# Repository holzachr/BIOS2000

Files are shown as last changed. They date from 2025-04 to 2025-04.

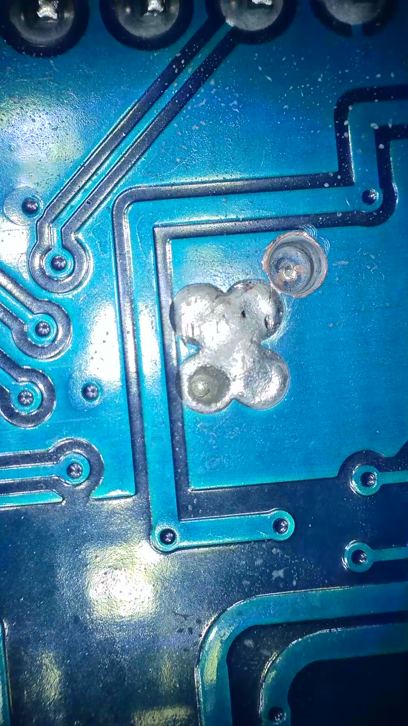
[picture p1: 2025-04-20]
Hardware/MFRC522 RFID module modification for I2C bus/MFRC522_I2C_mod_3.jpg

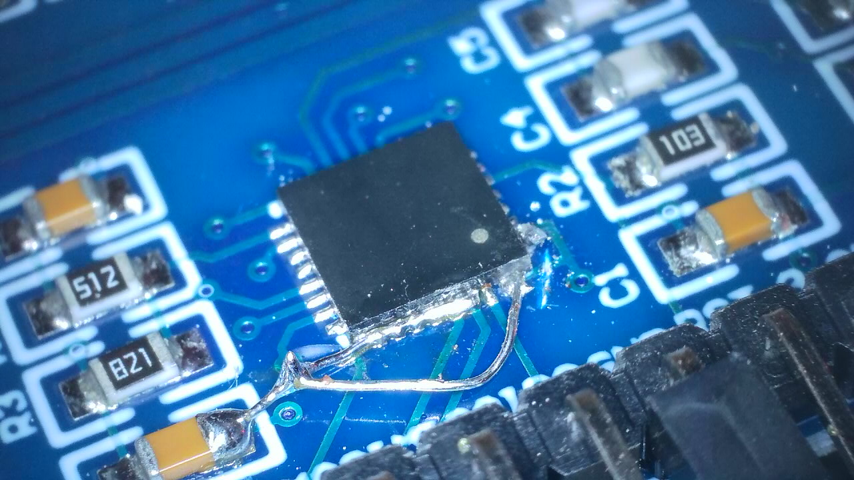
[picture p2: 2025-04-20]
Hardware/MFRC522 RFID module modification for I2C bus/MFRC522_I2C_mod_1.jpg

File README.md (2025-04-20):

# BIOS 2000
## An open-source cocktail machine and shot dispenser

- Peristaltic pumps are used to deliver liquids from bottles, 6 in this case, through 3x5 mm (inner and outer diameter) silicon hoses to an output.
- A simple web interface can be used to compose mixed drinks or just dispense shots.
- An RFID reader offers an "instant shot mode" after the tag has been read and a button pressed.

## Hardware

Main controller of this project is an ESP8266 "NodeMCU" module, programmed through the Arduino IDE.

The type G528 pumps are available in different sizes, 6 and 12 V, and different speeds. Because even the largest pump is quite slow in terms of typical drink volume, you want to get the biggest 150 ml/s 12 V variant.

Each two pumps are driven by a L298N H-bridge, and each H-Bridge is controlled by two GPIO lines.

To save GPIO lines from the ESP module, PCF8574 I2C-to-GPIO expanders are used, but this is generally optional.

The MFRC522 RFID reader modules generally only support SPI modes, but can be modified in order to use their I2C bus. This requires some fine soldering skills - check out the "Hardware" directory.

A LED strip offers fancy lighting.

Because my machine case is an old PC case, I repurposed the HDD activity LED to flicker randomly when the machine is working.

## ESP/Arduino libraries

- https://github.com/me-no-dev/ESPAsyncWebServer for the web server
- https://github.com/me-no-dev/ESPAsyncTCP for WebSocket
- https://github.com/bblanchon/ArduinoJson for data exchange between Arduino and web code
- https://github.com/RobTillaart/PCF8574/ for the IO expanders
- https://github.com/arozcan/MFRC522-I2C-Library/ for the RFID reader
- https://github.com/FastLED/FastLED for an optional LED strip

## Pump calibration

The pump variation is quite large, and you want to make sure that the drinks don't spill over.
That's what the calibration.html website on the ESP is for:
You dispense a drink, say 300 ml, from each pump. You measure or weight how much you actually got, and use the calibration.html website to calculate individual per-pump ml/s values, which are compiled into the code (nasty).
Make sure you adapt those constants to your individual pumps.

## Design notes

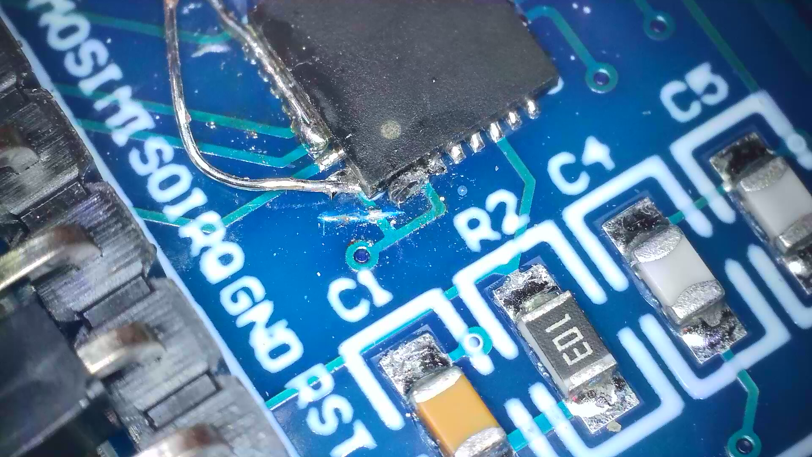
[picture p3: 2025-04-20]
Hardware/MFRC522 RFID module modification for I2C bus/MFRC522_I2C_mod_2.jpg

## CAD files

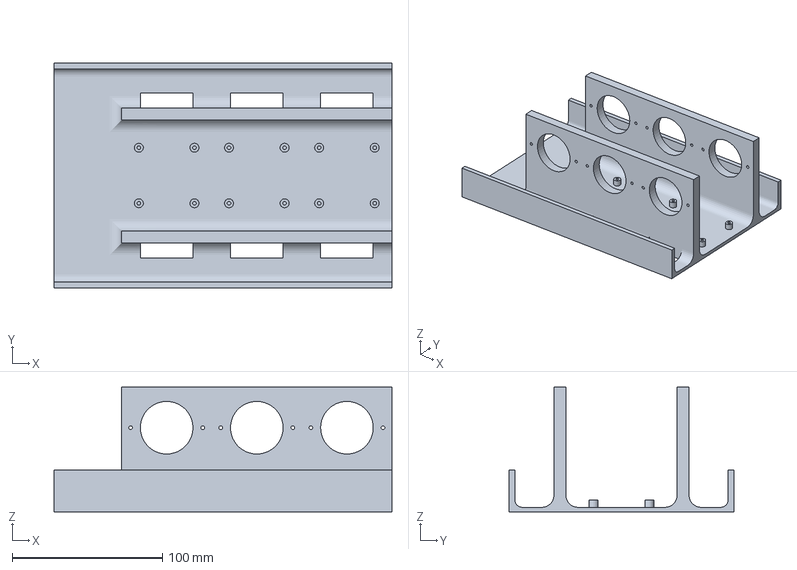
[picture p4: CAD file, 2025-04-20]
Hardware/Cocktailautomat v4.3mf
225.0 x 150.0 x 83.0 mm

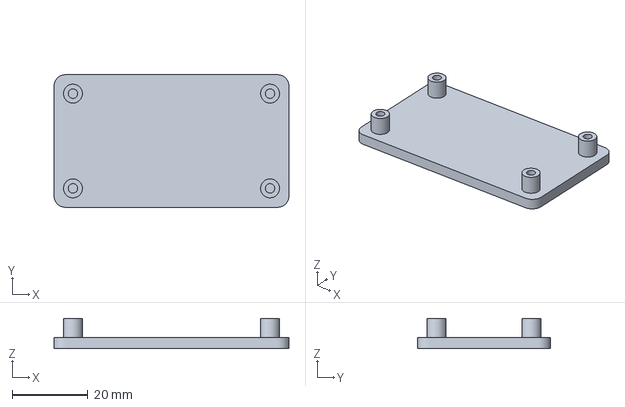
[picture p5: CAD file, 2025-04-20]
Hardware/Cocktailautomat NodeMCU Halter v1.3mf
62.0 x 35.0 x 8.00 mm

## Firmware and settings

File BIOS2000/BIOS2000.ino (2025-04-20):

#include <Arduino.h>            // From Arduino
#include <queue>                // From Arduino

#include <Wire.h>               // From Arduino / ESP8266 board package
#include <LittleFS.h>           // From Arduino / ESP8266 board package
#include <ESP8266WiFi.h>        // From Arduino / ESP8266 board package

#include <PCF8574.h>            // https://github.com/RobTillaart/PCF8574
#include <ESPAsyncWebServer.h>  // https://github.com/ESP32Async/ESPAsyncWebServer
#include <ArduinoJson.h>        // https://github.com/bblanchon/ArduinoJson
#include <MFRC522_I2C.h>        // https://github.com/arozcan/MFRC522-I2C-Library
#include <FastLED.h>            // https://github.com/FastLED/FastLED



// --- Pin configuration ---
#define RFID_RESET_PIN     D0   // RFID module reset pin. Required for library, but not used.
#define I2C_SDA_PIN        D1   // I2C bus SDA
#define I2C_SCL_PIN        D2   // I2C bus SCL
#define LED_STRIP_DATA_PIN D4   // WS2812B LED data  
#define ACTIVITY_LED_PIN   D5   // Activity LED
#define SHOT_BUTTON_PIN    D6   // Instant shot button, needs internal pull-up

// --- I2C bus device configuration ---
#define I2C_ADDRESS_PCF8474_IO_EXTENDER_1  0x20
#define I2C_ADDRESS_PCF8474_IO_EXTENDER_2  0x21
#define I2C_ADDRESS_MFRC522_RFID_READER    0x28

// --- WiFi AP configuration ---
const char *SSID = "PromilleProfi";
const char *WPA_PASSWORD = "12345679";

// IO extenders
PCF8574 Extender1(I2C_ADDRESS_PCF8474_IO_EXTENDER_1, &Wire);
PCF8574 Extender2(I2C_ADDRESS_PCF8474_IO_EXTENDER_2, &Wire);

// Pump hardware configuration struct
typedef struct
{
  PCF8574 * pPCF;               // Pointer to PCF8574 IO extender
  byte pin1;                    // Pin 1 of H-bridge, pin number on IO extender [0-7]
  byte pin2;                    // Pin 2 of H-bridge, pin number on IO extender [0-7]
  float mlPerSec;               // [ml/s] Flow rate
} tPumpHwConfig;

// --- Pump configuration ---
#define PUMP_COUNT              (6) // Number of pumps
#define ANTI_DRIP_REVERSE_MS   (30) // [ms] How long to pull back liquid to avoid dripping
String Ingredients[PUMP_COUNT];     
tPumpHwConfig PumpHwConfig[PUMP_COUNT] = 
{
// IO Extender  Pin1  Pin2  ml/s
  {&Extender1,  0,    1,    3.1000},   // Pump 0
  {&Extender1,  2,    3,    1.9024},   // Pump 1
  {&Extender1,  4,    5,    1.6946},   // ...
  {&Extender1,  6,    7,    2.6083},   // ...
  {&Extender2,  0,    1,    1.9389},   // ...
  {&Extender2,  2,    3,    1.8174},   // Pump 5
};

// --- Instant shot push button ---
#define SHOT_AMOUNT_ML     20   // [ml] Amount to dispense for instant shot
const char RFID_CARD_UIDs[PUMP_COUNT][7] =
{
  // Card UID
  {0x04, 0x31, 0xDB, 0x03, 0xC1, 0x2A, 0x81},  // This card UID selects pump 0
  {0x04, 0x32, 0xDB, 0x03, 0xC1, 0x2A, 0x81},  // This card UID selects pump 1
  {0x04, 0x33, 0xDB, 0x03, 0xC1, 0x2A, 0x81},  // This card UID selects pump 2
  {0x04, 0x34, 0xDB, 0x03, 0xC1, 0x2A, 0x81},  // This card UID selects pump 3
  {0x04, 0x28, 0xDB, 0x03, 0xC1, 0x2A, 0x81},  // This card UID selects pump 4
  {0x04, 0x29, 0xDB, 0x03, 0xC1, 0x2A, 0x81},  // This card UID selects pump 5
};



AsyncWebServer server(80);  // Web server
AsyncWebSocket ws("/ws");   // WebSocket endpoint under "/ws"

// Struct for mix command
struct MixCommand 
{
  int pump;
  int amount;
};

// Queue for mix commands
std::queue<MixCommand> WorkQueue;

// Pump operation state struct
typedef struct
{
  unsigned long startTimeMs;
  unsigned long durationMs;  
  bool isMixing;
} tPumpState;

// Pump state
tPumpState PumpState[PUMP_COUNT] = {0, 0, false};

// RFID reader
MFRC522 mfrc522(I2C_ADDRESS_MFRC522_RFID_READER, RFID_RESET_PIN);

// --- LED strip configuration ---
#define LED_STRIP_TYPE           WS2812B
#define LED_STRIP_NUM_LEDS       34
#define LED_STRIP_COLOR_ORDER    GRB
#define LED_STRIP_BRIGHTNESS     90             // [0..255] Brightness
#define LED_STRIP_DELAY_IDLE_MS  50             // [ms] Time from change to change when idle, higher = slower
#define LED_STRIP_DELAY_BUSY_MS  6              // [ms] Time from change to change when mixing, higher = slower
CRGB LED_STRIP_LEDS[LED_STRIP_NUM_LEDS];
CRGBPalette16 LedStripPalette;
TBlendType    LedStripBlending;



void loadIngredientsFromFile() 
{
  File file = LittleFS.open("/ingredients.json", "r");
  if (!file) 
  {
    Serial.println("Error: ingredients.json not found! Setting default values...");
       
    // Default values
    for (int p = 0; p < PUMP_COUNT; p++)
      Ingredients[p] = "Empty";

    return;
  }

  StaticJsonDocument<256> doc;
  DeserializationError error = deserializeJson(doc, file);
  file.close();

  if (error) 
  {
    Serial.println("Error reading ingredients.json! Setting default values...");
    return;
  }

  // Apply values from JSON
  for (int i = 0; i < PUMP_COUNT; i++) 
  {
    Ingredients[i] = doc["pumps"][String(i + 1)].as<String>();
  }

  Serial.println("Ingredients configuration loaded:");
  for (int i = 0; i < PUMP_COUNT; i++) 
  {
    Serial.printf("Pumpe %d: %s\n", i + 1, Ingredients[i].c_str());
  }
} // loadIngredientsFromFile()

void saveIngredientsToFile() 
{
  StaticJsonDocument<256> doc;
    
  for (int i = 0; i < PUMP_COUNT; i++) 
  {
    doc["pumps"][String(i + 1)] = Ingredients[i];
  }

  File file = LittleFS.open("/ingredients.json", "w");
  if (!file) 
  {
    Serial.println("Error saving ingredients configuration!");
    return;
  }

  serializeJson(doc, file);
  file.close();
  Serial.println("Ingredients configuration saved successfully!");
} // saveIngredientsToFile()

String loadRecipesFromFile() 
{
  if (!LittleFS.exists("/recipes.json")) 
  {
    return "{}";  // Return empty JSON if file does not exist
  }
  File file = LittleFS.open("/recipes.json", "r");
  if (!file) 
  {
    return "{}";
  }
  String json = file.readString();
  file.close();
  return json;
} // loadRecipesFromFile()

void saveRecipesToFile(String json) 
{
  File file = LittleFS.open("/recipes.json", "w");
  if (!file) 
  {
    Serial.println("Error saving recipes!");
    return;
  }
  file.print(json);
  file.close();
} // saveRecipesToFile()

void handleSaveRecipe(AsyncWebServerRequest *request) 
{
  if (request->hasParam("data", true)) 
  {
    String json = request->getParam("data", true)->value();
    saveRecipesToFile(json);
    request->send(200, "text/plain", "Saved");
  } 
  else 
  {
    request->send(400, "text/plain", "Missing data");
  }
} // handleSaveRecipe()

// Send message to all WebSocket clients
void notifyClients(String message) 
{
    ws.textAll(message);
}

void onWebSocketEvent(AsyncWebSocket *server, AsyncWebSocketClient *client, AwsEventType type, void *arg, uint8_t *data, size_t len) 
{
    if (type == WS_EVT_CONNECT) 
    {
        Serial.println("WebSocket client connected!");
    }
} // onWebSocketEvent()

void handleSaveIngredients(AsyncWebServerRequest *request) 
{
  for (int i = 0; i < PUMP_COUNT; i++) 
  {
    String paramName = "p" + String(i + 1);
    if (request->hasParam(paramName)) 
    {
      Ingredients[i] = request->getParam(paramName)->value();
    }
  }

  saveIngredientsToFile();

  // Send WebSocket notification to clients
  notifyClients("update");

  request->send(200, "text/plain", "Ingredients configuration saved!");
} // handleSaveIngredients()

void handleGetIngredients(AsyncWebServerRequest *request) 
{
  StaticJsonDocument<512> doc;
  doc["pump_count"] = PUMP_COUNT;

  for (int i = 0; i < PUMP_COUNT; i++) 
  {
    doc["pumps"][String(i + 1)] = Ingredients[i];  // Ingredients-to-pump assignment
  }

  String jsonResponse;
  serializeJson(doc, jsonResponse);
    
  request->send(200, "application/json", jsonResponse);
} // handleGetIngredients()

void handleGetCalibration(AsyncWebServerRequest *request) 
{
  String jsonString = "[";
  for (int i = 0; i < PUMP_COUNT; i++) 
  {
    jsonString += String(PumpHwConfig[i].mlPerSec);
    if (i < PUMP_COUNT - 1) 
      jsonString += ", ";
  }
  jsonString += "]";
  request->send(200, "application/json", jsonString);
} // handleGetCalibration()

void pumpStop(int pump)
{
  if (pump >= PUMP_COUNT)
    return;

  PumpHwConfig[pump].pPCF->write(PumpHwConfig[pump].pin1, LOW);
  PumpHwConfig[pump].pPCF->write(PumpHwConfig[pump].pin2, LOW);
} // pumpStop()

void pumpForward(int pump)
{
  if (pump >= PUMP_COUNT)
    return;

  PumpHwConfig[pump].pPCF->write(PumpHwConfig[pump].pin1, LOW);
  PumpHwConfig[pump].pPCF->write(PumpHwConfig[pump].pin2, LOW);
  
  // Safety delay to not short-circuit the H-bridge
  delay(2); 
  
  PumpHwConfig[pump].pPCF->write(PumpHwConfig[pump].pin1, HIGH);
  PumpHwConfig[pump].pPCF->write(PumpHwConfig[pump].pin2, LOW);
} // pumpForward()

void pumpReverse(int pump)
{
  if (pump >= PUMP_COUNT)
    return;

  PumpHwConfig[pump].pPCF->write(PumpHwConfig[pump].pin1, LOW);
  PumpHwConfig[pump].pPCF->write(PumpHwConfig[pump].pin2, LOW);
  
  // Safety delay to not short-circuit the H-bridge
  delay(2); 
  
  PumpHwConfig[pump].pPCF->write(PumpHwConfig[pump].pin1, LOW);
  PumpHwConfig[pump].pPCF->write(PumpHwConfig[pump].pin2, HIGH);
} // pumpReverse()

bool isMixing()
{
  for (int p = 0; p < PUMP_COUNT; p++)
  {
    if (PumpState[p].isMixing)
    {
      return true;
    }
  }

  return false;
} // isMixing()

void mixCocktail(AsyncWebServerRequest *request, uint8_t *data, size_t len, size_t index, size_t total) 
{
  DynamicJsonDocument doc(512);
  DeserializationError error = deserializeJson(doc, data, len);

  if (error) 
  {
    request->send(400, "application/json", "{\"status\": \"JSON error\"}");
    return;
  }

  if (isMixing())
  {
    request->send(400, "application/json", "{\"status\": \"Busy\"}");
    return;
  }

  // Parse recipe and enqueue pump work
  for (JsonObject elem : doc.as<JsonArray>()) 
  {
    int pump = elem["pump"];
    int amount = elem["amount"];        
    WorkQueue.push({pump - 1, amount});  // Pumps count from 0 in C++
  }

  request->send(200, "application/json", "{\"status\": \"Mixing cocktail\"}");
}

void handleStop(AsyncWebServerRequest *request) 
{
  for (int p = 0; p < PUMP_COUNT; p++)
  {
    if (PumpState[p].isMixing)
    {
      PumpState[p].durationMs = 0;
    }
  }
  
  request->send(200, "text/plain", "Stopping");
} // mixCocktail()

void showActivityLed()
{
  static unsigned long startTimeMs = 0;
  static unsigned long durationMs = 0;
  static bool ledOn = false;
  static bool lastIsMixing = false;

  if (isMixing() && !lastIsMixing)        // Mixing just started:
  {
    lastIsMixing = true;
    digitalWrite(ACTIVITY_LED_PIN, HIGH);   
    durationMs = random(300);
    ledOn = true;
    startTimeMs = millis();     
  }
  else if (isMixing() && lastIsMixing)    // Still mixing:
  {
    if (ledOn && (millis() - startTimeMs >= durationMs))
    {
      digitalWrite(ACTIVITY_LED_PIN, LOW);    // Turn off for random time 0..80 ms
      durationMs = random(200);
      ledOn = false;
      startTimeMs = millis();
    }
    else if (!ledOn && (millis() - startTimeMs >= durationMs))
    {
      digitalWrite(ACTIVITY_LED_PIN, HIGH);   // Turn on for random time 0..300 ms
      durationMs = random(300);
      ledOn = true;
      startTimeMs = millis();
    }
    else
    {
      // Stay in on/off state
    }
  }
  else if (!isMixing() && lastIsMixing)   // Mixing just finished:
  {
    // Turn everything off
    digitalWrite(ACTIVITY_LED_PIN, LOW);      // Turn off
    ledOn = false;
  }
  else
  {
    // Never the case
  }
} // showActivityLed()

void showRFIDReaderDetails() 
{
  // Get the MFRC522 software version
  byte version = mfrc522.PCD_ReadRegister(mfrc522.VersionReg);
  Serial.printf("MFRC522 software version: 0x%2.2X\n", version);

  // When 0x00 or 0xFF is returned, communication probably failed
  if ((version == 0x00) || (version == 0xFF)) 
  {
    Serial.println(F("WARNING: Communication failure, is the MFRC522 properly connected?"));
  }
} // showRFIDReaderDetails() 
  
void readRFIDCardAndDispenseInstantShot()
{
  if (!isMixing() && (digitalRead(SHOT_BUTTON_PIN) == LOW))
  {
    // Look for new cards, and select one if present
    if (mfrc522.PICC_IsNewCardPresent() && mfrc522.PICC_ReadCardSerial()) 
    {
      int pump = PUMP_COUNT;
      bool pumpFound = false;

      Serial.println("RFID card found.");

      for (int p = 0; p < PUMP_COUNT; p++)
      {
        for (int i = 0; i < mfrc522.uid.size; i++)
        {
          if (RFID_CARD_UIDs[p][i] != mfrc522.uid.uidByte[i])
          {
            break;
          }
          else if (i == (mfrc522.uid.size-1) && RFID_CARD_UIDs[p][i] == mfrc522.uid.uidByte[i])
          {
            pumpFound = true;
            pump = p;
          }
        }
      }

      if (pumpFound)   
      {
        Serial.printf("Dispensing shot from pump %d\n", pump);
        WorkQueue.push({pump, SHOT_AMOUNT_ML});
      }
    }
  }
} // readRFIDCardAndDispenseInstantShot()

void setLedStrip()
{
  static unsigned long startTimeMs = millis();
  static unsigned long durationMs = LED_STRIP_DELAY_IDLE_MS;
  static bool lastIsMixing = false;

  static uint8_t startIndex = 0;
  if ((millis() - startTimeMs) >= durationMs)
  {
    startTimeMs = millis();
    startIndex = startIndex + 1; /* motion speed */
    FillLEDsFromPaletteColors(startIndex, !isMixing());
  }  
  
  FastLED.show();

  if (isMixing() && !lastIsMixing)        // Mixing just started:
  {
    lastIsMixing = true;
    durationMs = LED_STRIP_DELAY_BUSY_MS; 
    LedStripSetMixingPalette();
  }
  else if (!isMixing() && lastIsMixing)   // Mixing just finished:
  {
    lastIsMixing = false;
    durationMs = LED_STRIP_DELAY_IDLE_MS; 
    LedStripSetIdlePalette();
  }
  else
  {
    // Never the case
  }
} // setLedStrip()

// This function sets the next LED strip state
void FillLEDsFromPaletteColors(uint8_t colorIndex, bool lightTheBase)
{ 
  // Set palette for all LEDs
  for (int i = 0; i < LED_STRIP_NUM_LEDS; i++) 
  {
    LED_STRIP_LEDS[i] = ColorFromPalette(LedStripPalette, colorIndex, LED_STRIP_BRIGHTNESS, LedStripBlending);
    colorIndex += 3;
  }

  if (lightTheBase)
  {
    // First and last LED pure white to light the case neutrally
    LED_STRIP_LEDS[0] = CRGB::White;
    LED_STRIP_LEDS[1] = CRGB::White;
    LED_STRIP_LEDS[LED_STRIP_NUM_LEDS-1] = CRGB::White;
  }
}

void LedStripSetIdlePalette()
{
  CRGB yellow = CHSV(HUE_YELLOW, 255, 255);
  CRGB orange = CHSV(HUE_ORANGE, 255, 255);
  CRGB red  = CHSV(HUE_RED, 255, 255);
    
  LedStripPalette = CRGBPalette16(
                                 yellow, orange, red, orange,
                                 yellow, orange, red, orange,
                                 yellow, orange, red, orange,
                                 yellow, orange, red, orange );

  LedStripBlending = LINEARBLEND;  
}

void LedStripSetMixingPalette()
{
  // This function fills the LED strip palette with totally random colors.
  for (int i = 0; i < 16; i++) 
  {
    LedStripPalette[i] = CHSV(random8(), 255, random8());
  }

  LedStripBlending = NOBLEND;
}

void setup() 
{
	Serial.begin(115200);

  Wire.begin(I2C_SDA_PIN, I2C_SCL_PIN);

  pinMode(ACTIVITY_LED_PIN, OUTPUT);
  digitalWrite(ACTIVITY_LED_PIN, LOW);

  pinMode(SHOT_BUTTON_PIN, INPUT_PULLUP);

  mfrc522.PCD_Init();
  showRFIDReaderDetails();

  for (int p = 0; p < PUMP_COUNT; p++)
  {
    if (!PumpHwConfig[p].pPCF->begin(0x00))
    {
      Serial.println("could not initialize...");
    }
    if (!PumpHwConfig[p].pPCF->isConnected())
    {
      Serial.println("=> not connected");
      //while(1);
    }
  }

  // Start Access Point
  WiFi.softAP(SSID, WPA_PASSWORD);
  Serial.println("Access Point started");

  if (!LittleFS.begin()) 
  {
    Serial.println("Error loading filesystem");
    return;
  }
  else 
  {
    Serial.println("LittleFS loaded successfully");
  }

  Dir dir = LittleFS.openDir("/");
  while (dir.next()) 
  {
    Serial.println("Found file: " + dir.fileName());
  }

  loadIngredientsFromFile();

  // Cocktails user page
  server.on("/", HTTP_GET, [](AsyncWebServerRequest *request) 
  {
    request->send(LittleFS, "/cocktails.html", "text/html");
  });
  server.on("/cocktails", HTTP_GET, [](AsyncWebServerRequest *request) 
  {
    request->send(LittleFS, "/cocktails.html", "text/html");
  });

  // Shots user page
  server.on("/shots", HTTP_GET, [](AsyncWebServerRequest *request) 
  {
    request->send(LittleFS, "/shots.html", "text/html");
  });
  
  // Admin page (Ingredients configuration)
  server.on("/zutaten", HTTP_GET, [](AsyncWebServerRequest *request) 
  {
    request->send(LittleFS, "/admin.html", "text/html");
  });
  server.serveStatic("/positions.png", LittleFS, "/positions.png");

  // Calibration page
  server.on("/calibration", HTTP_GET, [](AsyncWebServerRequest *request) 
  {
    request->send(LittleFS, "/calibration.html", "text/html");
  });

  // Load saved recipes JSON
  server.on("/getRecipes", HTTP_GET, [](AsyncWebServerRequest *request)
  {
    request->send(200, "application/json", loadRecipesFromFile());
  });

  // Show and upload files to LittleFS
  server.on("/files", HTTP_GET, [](AsyncWebServerRequest *request) {
    request->send(LittleFS, "/upload.html", "text/html");
  });

  server.on("/saveRecipe", HTTP_POST, handleSaveRecipe);
  server.on("/getCalibration", HTTP_GET, handleGetCalibration);
  server.on("/getIngredients", HTTP_GET, handleGetIngredients);
  server.on("/saveIngredients", HTTP_GET, handleSaveIngredients);    
  server.on("/mixCocktail", HTTP_POST, [](AsyncWebServerRequest *request) {}, NULL, mixCocktail);
  server.on("/stop", HTTP_POST, handleStop);
  
  // Upload file to LittleFS
  server.on(
    "/uploadFile", HTTP_POST,
    [](AsyncWebServerRequest *request) 
    {
      request->send(200, "text/plain", "Upload successful!");
    },
    [](AsyncWebServerRequest *request, String filename, size_t index, uint8_t *data, size_t len, bool final) 
    {
      static File uploadFile;
      
      if (index == 0) 
      {
        Serial.printf("Upload started: %s\n", filename.c_str());
        uploadFile = LittleFS.open("/" + filename, "w");
      }

      if (uploadFile) 
      {
        uploadFile.write(data, len);
      }

      if (final) 
      {
        Serial.printf("Upload finished: %s (%u Bytes)\n", filename.c_str(), index + len);
        uploadFile.close();
      }
    }
  );

  // List LittleFS files
  server.on("/listFiles", HTTP_GET, [](AsyncWebServerRequest *request) {
    String output = "<h3>Inhalt von LittleFS:</h3><ul>";
    File root = LittleFS.open("/", "r");
    File file = root.openNextFile();
    while (file) 
    {
      output += "<li>" + String(file.name()) + " (" + String(file.size()) + " Bytes)</li>";
      file = root.openNextFile();
    }
    output += "</ul>";
    request->send(200, "text/html", output);
  });

  // Start WebSocket
  ws.onEvent(onWebSocketEvent);
  server.addHandler(&ws);

  // Start webserver  
  server.begin();

  // Start LED strip
  FastLED.addLeds<LED_STRIP_TYPE, LED_STRIP_DATA_PIN, LED_STRIP_COLOR_ORDER>(LED_STRIP_LEDS, LED_STRIP_NUM_LEDS).setCorrection(TypicalLEDStrip);
  FastLED.setBrightness(LED_STRIP_BRIGHTNESS);
  LedStripSetIdlePalette();
} // setup()

void loop() 
{
  // --- Handle new dispense commands ---
  // One pump is started per loop() run.
  // This is to distribute the startup current.
  if (!WorkQueue.empty())
  {
    MixCommand cmd = WorkQueue.front();
    Serial.printf("Request: Pump %d with %d ml\n", cmd.pump, cmd.amount);

    // Checks
    if (cmd.pump >= PUMP_COUNT)         // Invalid pump number
    {
      WorkQueue.pop();                  // Remove illegal command anyway
      return;
    }
    if (PumpState[cmd.pump].isMixing)   // Pump already busy
    {
      WorkQueue.pop();                  // Remove illegal command anyway
      return;
    }
    
    // Start dispensing
    PumpState[cmd.pump].durationMs = (int)(((float)cmd.amount * 1000) / (PumpHwConfig[cmd.pump].mlPerSec));

    Serial.printf("Pump %d forward for %d ms\n", cmd.pump, PumpState[cmd.pump].durationMs);

    PumpState[cmd.pump].startTimeMs = millis();
    pumpForward(cmd.pump);
    PumpState[cmd.pump].isMixing = true;
    
    WorkQueue.pop();                  // Remove successfully started item from work queue
  }

  // --- Watch and end ongoing dispenses ---
  for (int p = 0; p < PUMP_COUNT; p++)
  {
    if (PumpState[p].isMixing)
    {
      if (millis() - PumpState[p].startTimeMs >= PumpState[p].durationMs)
      {
        pumpStop(p);
        delay(5);
            
        // Pull back some liquid to avoid dripping
        pumpReverse(p);
        delay(ANTI_DRIP_REVERSE_MS);
        pumpStop(p);

        PumpState[p].isMixing = false;

        Serial.printf("Pump %d done.\n", p);
      }
    }
  }

  // --- Handle activity LED ---
  showActivityLed();

  // --- Watch instant shot button and RFID card reader ---
  readRFIDCardAndDispenseInstantShot();

  // --- Handle WebSocket clients ---
  ws.cleanupClients();

  // --- Handle LED strip ---
  setLedStrip();
} // loop()
